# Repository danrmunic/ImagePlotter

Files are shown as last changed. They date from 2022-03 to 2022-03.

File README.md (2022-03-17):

# Image Plotter
__Authors: John Bennett, Daniel Munic, Rudi Diaz__<br />
__Date Modified: March 15, 2022__

This README.md introduces the Image Plotter project, a ME 405 project. It includes the overviews of the implemented hardware and software as well as aa discussion of the results and what we have learned.

## Introduction
We created an image plotter capable of moving a pen with 2.5 degrees of freedom The robot plots in polar (r, theta) coordinates and can turn its operation on and off, by lifting or dropping a pen. We rotate a threaded rod for radial translations and use direct drive to move our wheel around a fixed origin to create the theta angle. A solenoid was used for lifting a pen. We communicate drawing instruction through the serial port from our PC. 

The project is intended to be operated by its creators: John Bennett, Daniel Munic, and Rudi Diaz since we have a deeper understanding of the code. But the device is intended for anyone that wants to use our image plotter. We have a file that converts an image into a printable text file that can be interpreted by our code. So, if anyone has an image, we can print it!

The goal of this project was to create any desired image by generating a series of contours and sending individual commands to the robot until the masterpiece is done. We were able demonstrate that we accomplished this goal by drawing squares, circles and writing the word image.

## Hardware Design Overview
The image plotter hardware that is structural consists of a support bearing, a wooden bearing, a wooden frame, a wooden leg for bearing, and a rod at the origin. The image plotter hardware that is non-structural consists of two Pitterson DC motors, a threaded rod, a direct drive shaft connected to a wheel, a sharpie, a breadboard, a 5A MOSFET, a solenoid, a Nucleo with a shoe, a 2 H-bridge motor driver, a limit switch, and a solenoid and pen carriage. For a full list of our hardware see the BOM below.

### BOM 
| Qty. | Part | Source | Est. Cost | 
|:----:|:---|:---|:---:|
|  2 | Pittperson Gearmotors | ME405 Tub | - |
|  1 | Nucleo with Shoe | ME405 Tub | - |
|  2 | Black Sharpie | Pre-Owned | - |
|  1 | Motor Driver 2 H-bridges  | ME405 Tub | - |
|  1 | 5A Power MOSFETs | [DigiiKey](https://www.digikey.com/en/products/detail/stmicroelectronics/STN3NF06L/654517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) | $3.80 |
|  1 | Diode | ME405 Tub | - |
|  1 | Solenoid Actuator | [Digikey](https://www.digikey.com/en/products/detail/sparkfun-electronics/ROB-11015/6163694) | $4.95 |
|  1 | Limit Switch | Gift | - |
|  1 | 1/4” Guide Rod 12” Long | ME405 Bin | - |
|  1 | 1/4” Threaded Rod 12” Long| ME405 Bin | - |
|  1 | 3” Rubber Wheel | ME405 Bin | - |
|  2 | 3/8 to 1/4 Shaft Coupler  | [amazon](https://www.amazon.com/Stainless-Steel-Screw-Shaft-Coupler/dp/B00KVNA50G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) | $9.98 |
|  1 | Bearing Wheel | Clayton | - |
|  1 | Wooden Bearings | Scrap Wood Bin | - |
|  1 | Wooden Frame | Scrap Wood Bin | - |
|  1 | Wooden Wheel Leg | Scrap Wood Bin | - |
|  1 | Rotating Rod at Origin | ME405 Bin | - |
|  1 | Solenoid and pen platform Carriage | 3D Print | - |

The motors are in charge of moving the solenoid and pen carriage. The pen carriage contains the sharpie and solenoid. One motor controls the radial distance by rotating the threaded shaft. This pushes the solenoid and pen carriage along the shaft at about motor 1000 radians per about 8 inches of radial movement. The solenoid and pen carriage uses the direct drive shaft and wooden bearings to keep movement stable. The second motor controls the angular coordinate by using direct drive to move the wheel around a fixed rod at the origin to create the theta angle, 20 radians on the motor are a 90 degree turn. We are also able to control the pen's linear motion, up and down, by using a solenoid. This allows the device to be able to draw on all areas of the paper. The solenoid is controlled by a MOSFET. When there is a high voltage input, the MOSFET will allow current to flow from 5V to ground. We have a diode in parallel with the solenoid to protect our handwear. The breadboard is used to provide a surface to connect electrical components. We have a limit switch which is mounted close to our motors. the limit switch allows up to locate the origin when the solenoid and pen carriage crash into it. The wooden frame is what everything is mounted to, and it provides support for the entire system. The support bearing adds another contact point to prevent the wooden frame from tilting. See figure 1 and 2 for hardware models. 

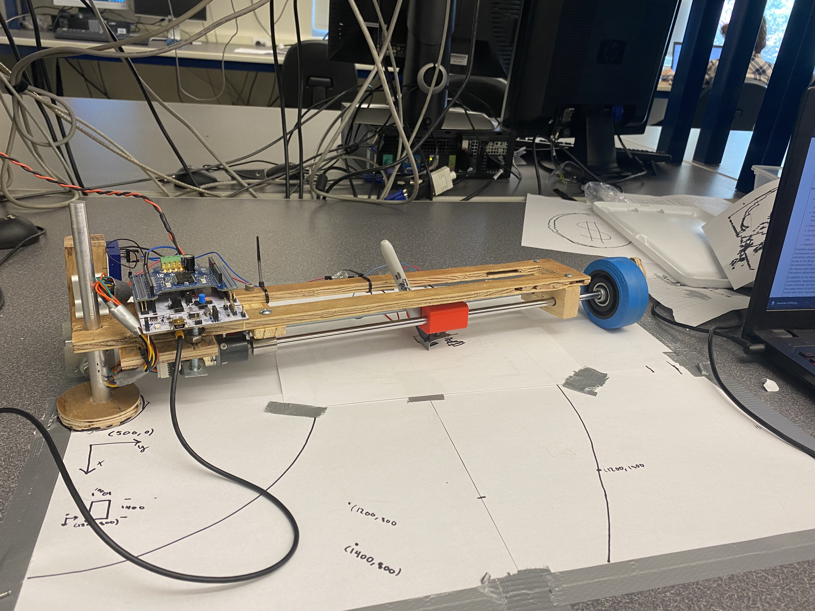
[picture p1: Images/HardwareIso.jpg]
Handwear


__Figure 1:__ Image Plotter Hardware.

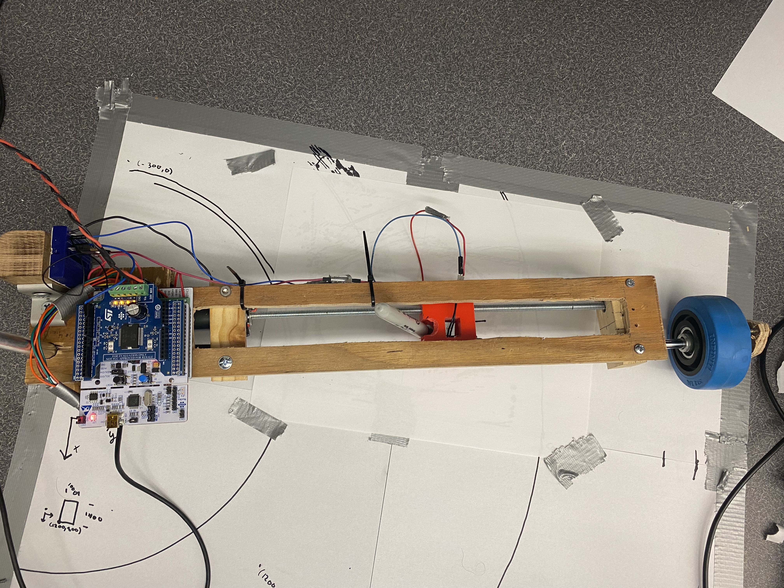
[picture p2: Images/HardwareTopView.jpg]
Top View Handwear


__Figure 2:__ Top View of Image Plotter Hardware.

Figure 3 shows a close-up view of our nucleo and breadboard and shows our wiring layout.

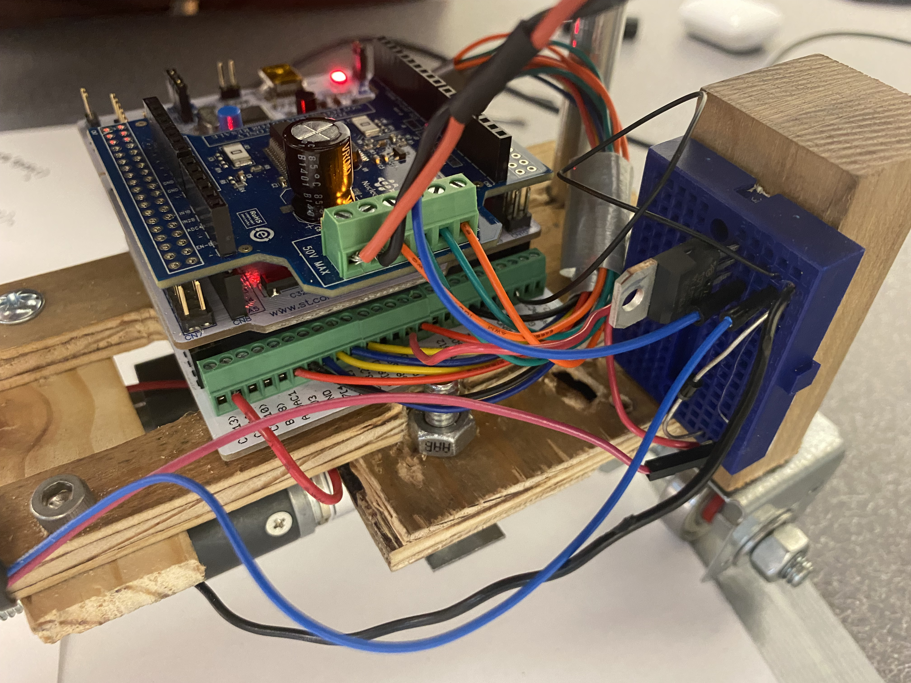
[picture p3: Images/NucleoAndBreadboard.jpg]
Nucleo and Breadboard Layout


__Figure 3:__ Top View of Image Plotter Hardware.

## Software Design Overview
The software ran on the nucleo is designed using a number of generators which operate as tasks scheduled in [main.py](https://github.com/danrmunic/ImagePlotter/blob/main/src/main.py). These tasks are the motor task, user task, logic task, and solenoid task. The code ran in [main.py](https://github.com/danrmunic/ImagePlotter/blob/main/src/main.py) is meant to accept a singular rectangular coordinate from the user and convert them into motor angles. Then the motors will send the solenoid to that location. By using serial port communication, we can continue to send new rectangular coordinates until we have fully drawn a picture. Besides accepting rectangular coordinates,our code will also accept up "{" and down "}" commands to control the solenoid.

The motor task sends both motors to the desired position using a [motor_driver](https://github.com/danrmunic/ImagePlotter/blob/main/src/motor_driver.py) object and [ClosedLoop](https://github.com/danrmunic/ImagePlotter/blob/main/src/closedloop.py) object, as well as receiving the motor position using an [Encoder](https://github.com/danrmunic/ImagePlotter/blob/main/src/Encoder.py) object to check if a movement is finished. The user task receives points from the serial port which are sent from the computer in [PC.py](https://github.com/danrmunic/ImagePlotter/blob/main/src/PC.py) (and generated in [sobel.py](https://github.com/danrmunic/ImagePlotter/blob/main/src/sobel.py)). The logic task does the math to convert those points from rectangular coordinates to values which can be sent to the motors in the polar coordinate system. Finally, the Solenoid task moves the pen up and down while drawing based on input from the computer.  

Variables are shared between tasks using Shares and Queues in [task_share.py](https://github.com/danrmunic/ImagePlotter/blob/main/src/task_share.py)

## Results Overview
Our system was able to draw a successful rectangle, circle, and the word "IMAGE" legibly. These images matched our jpg image. We will describe our testing process as well as the tests we preformed

We first started with calculations to predicted how to move from a rectangular coordinate to motor angles. We needed relationships between motor angles to theta and radius, we got these values experimentally by moving the motors. Next, we checked if the robot could accept polar coordinates. We wanted to determine if the robot could move to the desired polar coordinate. We had to further tune parameters to get the accuracy we wanted. Once we have achieved polar coordinates, we then started inputting rectangular coordinates. Once we were confident in our robot’s ability to move from one point to the next we moved to drawing images. 

The system was first tested by sending a picture of a square. While drawing we noticed that when the machine had to draw short strokes, the machine was able to make precise movements and replicate it onto the paper. However, when we inputted large change in position the machine would have difficulty accurately creating this line. This might be because the machine is working in radial and angular coordinates, so it struggles to be able to make straight lines, since the movement in the theta direction is significantly larger than the radial movement. As we progressed with the project, we were able to change the step size to get the best results. 

We had the system draw three figures. The first was a simple rectangle picture the rectangle was drawn based on the png image in figure 4. Figure 5 shows our machine’s output drawing. As you can see, the image is not a perfect copy of the image in figure 4, this is due to the fact that due to the machine's coordinate system being cylindrical and has large controller gains. This allowed for slight discrepancies as the machine did it's best to copy the image but was unable to make perfect lines. However, the results are still pretty amazing as the image is easily recognizable to the original image.



__Figure 4:__ Png Image of a Rectangle

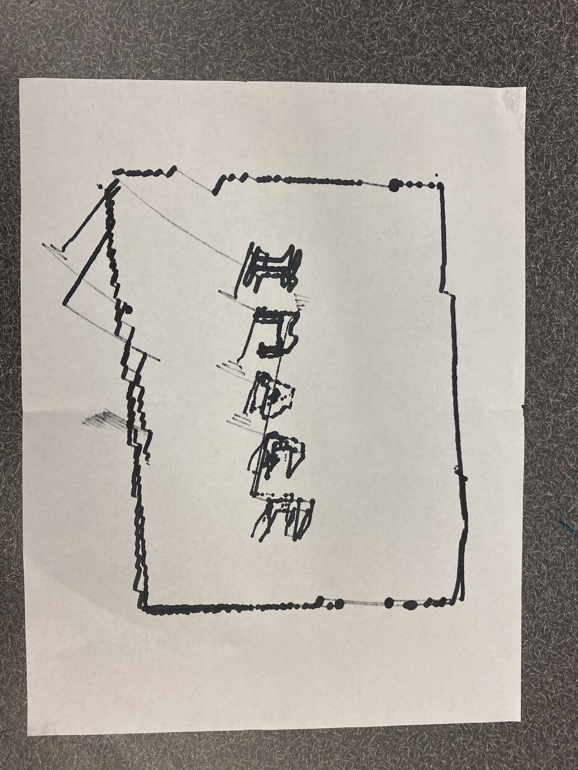
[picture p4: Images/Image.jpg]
Rectangle


__Figure 5:__ System's Drawing of a Rectangle. (Ignore the word image in the center)

We drew another simple shape of a circle. this drawing was also pretty good, but we did not have smooth curves. The scaling of the circle was obviously skewed. See figures 6 and 7. The image looked good and we were extremely happy with these results.

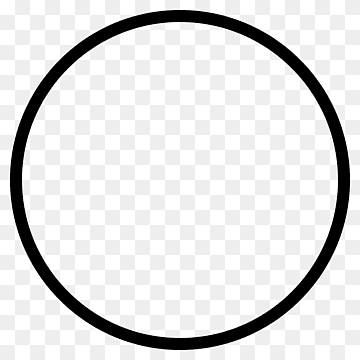
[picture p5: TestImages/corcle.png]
Circle Picture


__Figure 6:__ Png Image of a Circle.

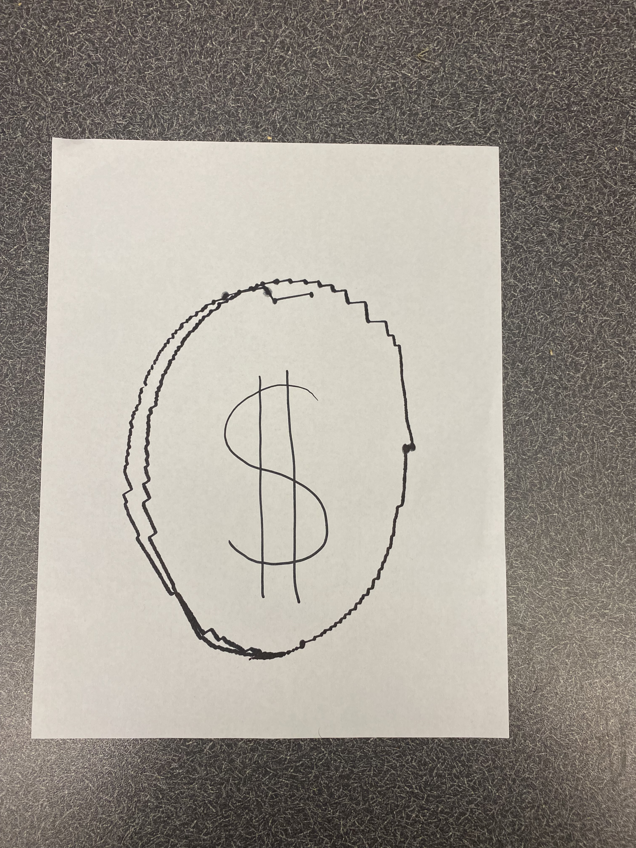
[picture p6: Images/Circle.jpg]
circle


__Figure 7:__ System's Drawing of a Circle.

The next image the machine drew was the word "IMAGE" as seen in figure 8. The drawing created by the robot can be seen in figure 9. Here we can see that the robot was able to replicate the drawing with a surprising amount of accuracy. One drawback was that machine took a large amount of time in order to complete this image as it could not move the pen at high speeds and the movements it made, while precise, were extremely small. We attempted to rectify this issue by having the machine draw every third point it received, but this led to errors, so we removed this feature. 



__Figure 8:__ Png Image of the Word Image.



__Figure 9:__ System's Drawing of the Word Image.

As for the last image, we had the image attempt to draw former US president Barack Obama. This was by far the most detailed image which unfortunately led to being the hardest one to complete. With all the details required, the image created unfortunately was not able to be an exact copy of the image we had. It also took a long time as the machine tried to capture every last detail. Our picture of Obama is unrecognisable.

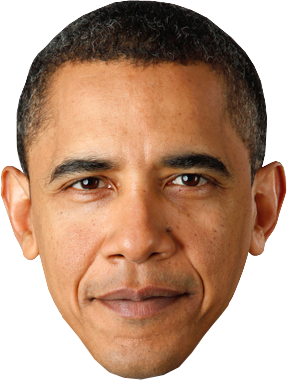
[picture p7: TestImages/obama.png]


__Figure 10:__ Png Image of Obama.

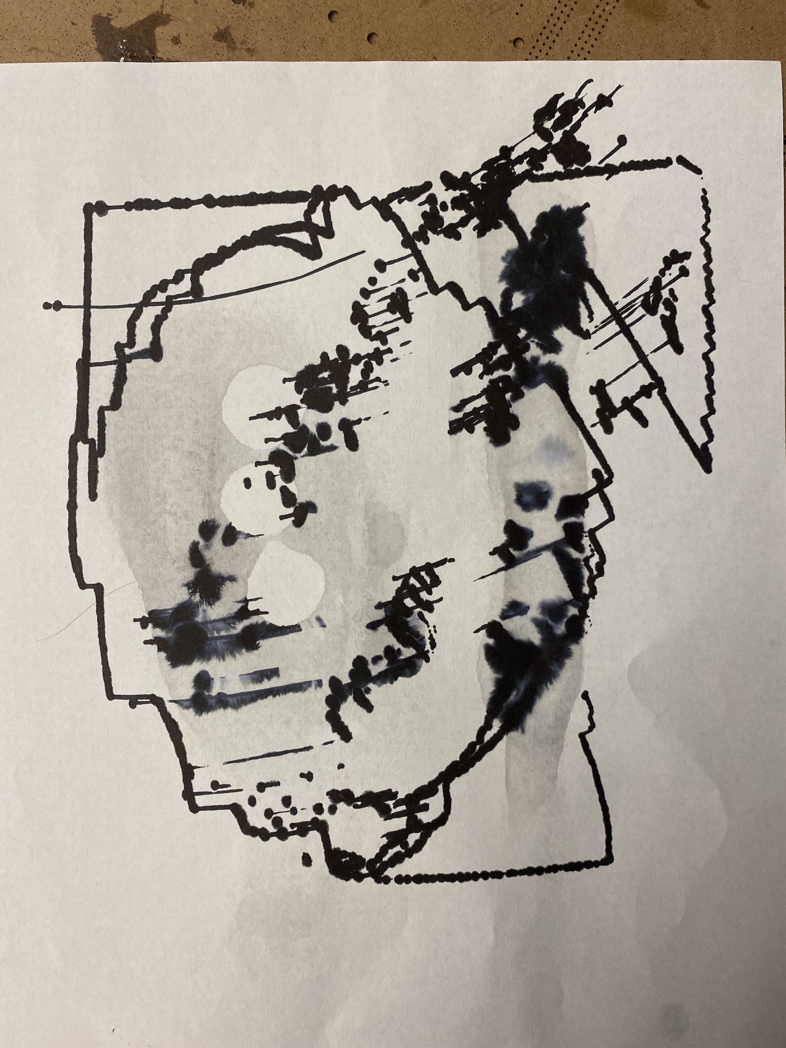
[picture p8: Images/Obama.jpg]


__Figure 11:__ System's Drawing of Obama.

## Expanding on the Process
In this project, we learned how useful it is to have a greater understanding of various components, we learned how to implement a limit switch, and a solenoid into our code. Also gaining experience and exploring different venders of mechatronic devices really opened our eyes to how to design. There were a couple of tough lessons that we learned during this project. The first was that when the robot rotated the motors moved at different speeds this made keeping a straight line difficult. To overcome this, we decreased the step size between movements. The next is that when purchasing an art make sure it can do what we want it to do. The purchased solenoid could not easily attach to the to the pen. There are solenoids that we could have bought with threads to mount stuff, but we failed to check for how it will mount. This error caused us a lot of stress since it took a long time for us to figure out how to hold the pen. Finally, our project was not the most well designed most of the arts were from the scrap bin, but by having good controls, good resolution and a well-tuned system helped to improve our systems performance in our project. 

For anyone who would like to build on our device, we have several recommendations could help. First, improve the way the solenoid is attached to the pen. Currently it is only attached by a quick solder. This allows the pen to rotate while drawing which ruins the accuracy of our lines. If the connection were rigid the pen would be able to draw more accurately. Additional parameter tuning is required to optimize the system the Ki and Kd are currently zero and the motor period and Kp could need more tuning. This would allow the drawing to get to each point more accurately and may even allow a decreased tolerance. Decreasing the number of points in a contour would greatly improve the speed at which the machine prints.  

## Additional files
### Microcontroller Classes

* [main.py](https://github.com/danrmunic/ImagePlotter/blob/main/src/main.py)
* [encoder.py](https://github.com/danrmunic/ImagePlotter/blob/main/src/Encoder.py)
* [motor_driver.py](https://github.com/danrmunic/ImagePlotter/blob/main/src/motor_driver.py)
* [closedloop.py](https://github.com/danrmunic/ImagePlotter/blob/main/src/closedloop.py)
* [task_share.py](https://github.com/danrmunic/ImagePlotter/blob/main/src/task_share.py)

### PC Classes
* [PC.py](https://github.com/danrmunic/ImagePlotter/blob/main/src/PC.py)
* [sobel.py](https://github.com/danrmunic/ImagePlotter/blob/main/src/sobel.py)

### Documentation

* [Image Plotter Documentation](https://github.com/danrmunic/ImagePlotter)

### Website Link

* [Image Plotter Website](https://danrmunic.github.io/ImagePlotter/index.html)

### Solidworks files

* [Solidworks files](https://github.com/danrmunic/ImagePlotter/tree/main/Solidworks%20Model)

### Images Used for Testing

* [TestImages](https://github.com/danrmunic/ImagePlotter/tree/main/TestImages)

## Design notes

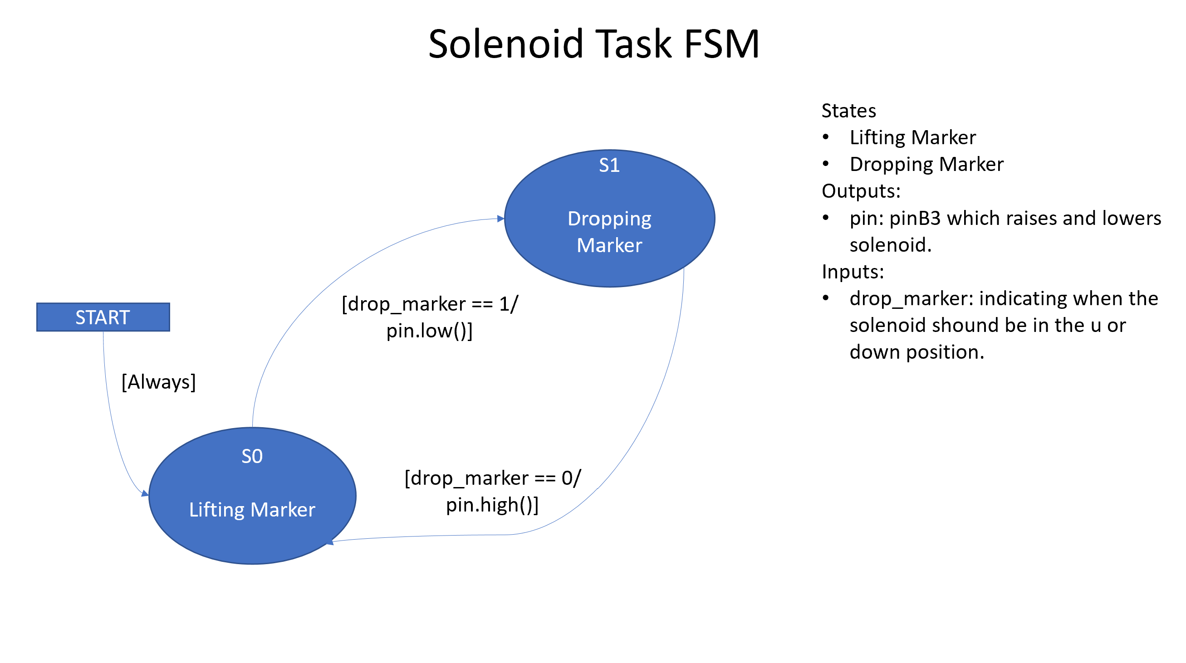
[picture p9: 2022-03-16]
Images/FSMSolenoid.png

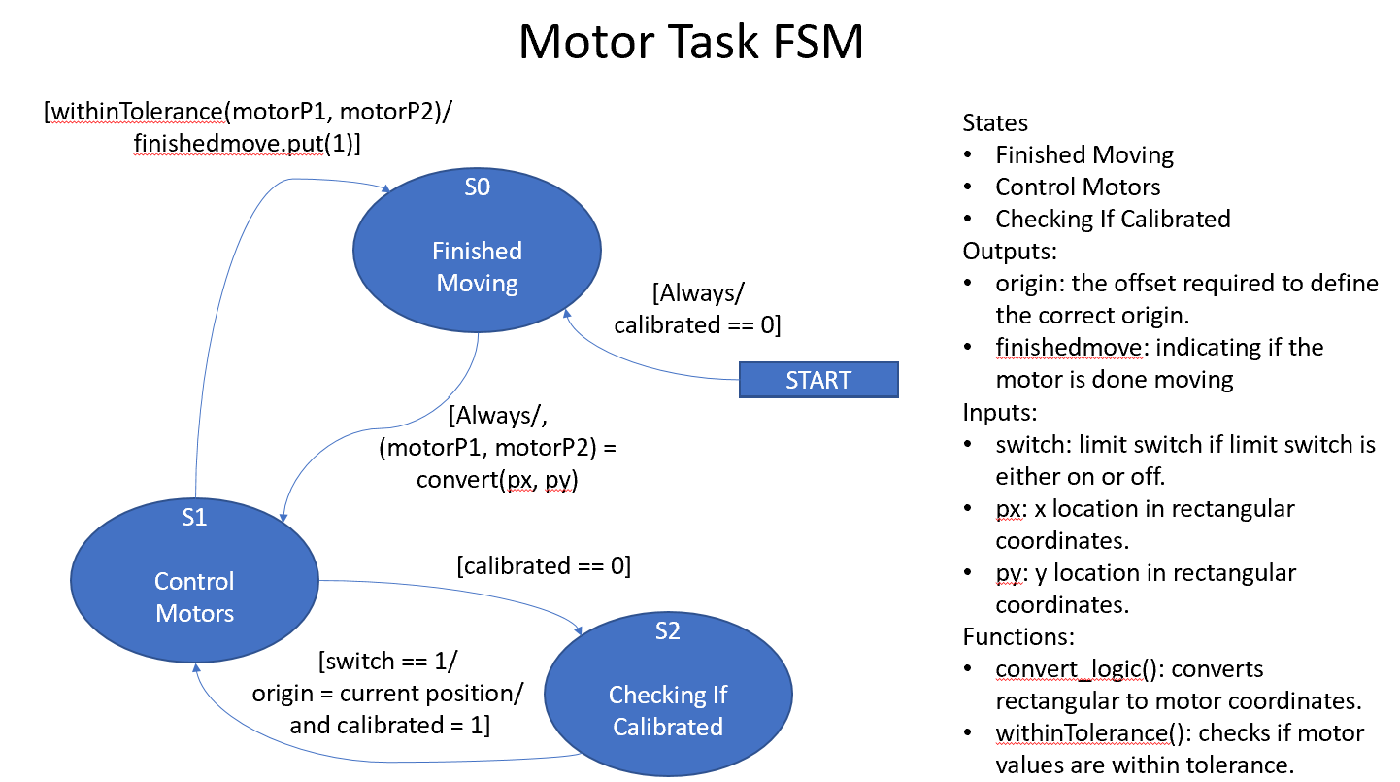
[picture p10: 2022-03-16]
Images/FSMMotors.png

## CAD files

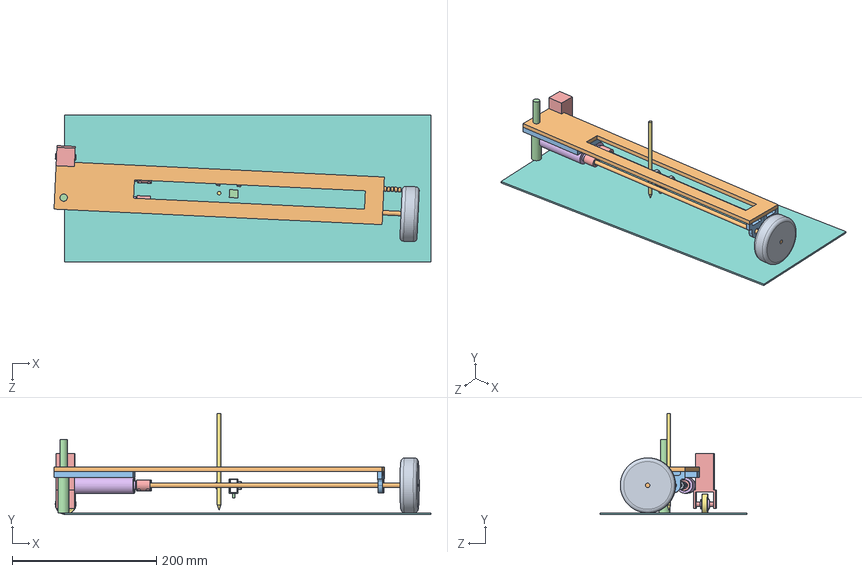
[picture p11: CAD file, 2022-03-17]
Solidworks Model/ImagePlotterFinalAssemble.SLDASM
522.4 x 140.5 x 203.2 mm
wheel
threaded shaft x 2
pillow block x 2
Solenoid
shaft coupler x 2
Patterson Motor x 2
pen
Paper^ImagePlotterFinalAssemble
95462A029_Medium-Strength Steel Hex Nut x 2
Part5^ImagePlotterFinalAssemble
Part1^ImagePlotterFinalAssemble
Part3^ImagePlotterFinalAssemble
Part4^ImagePlotterFinalAssemble
Bearing Spacer
60355K601_Ball Bearing

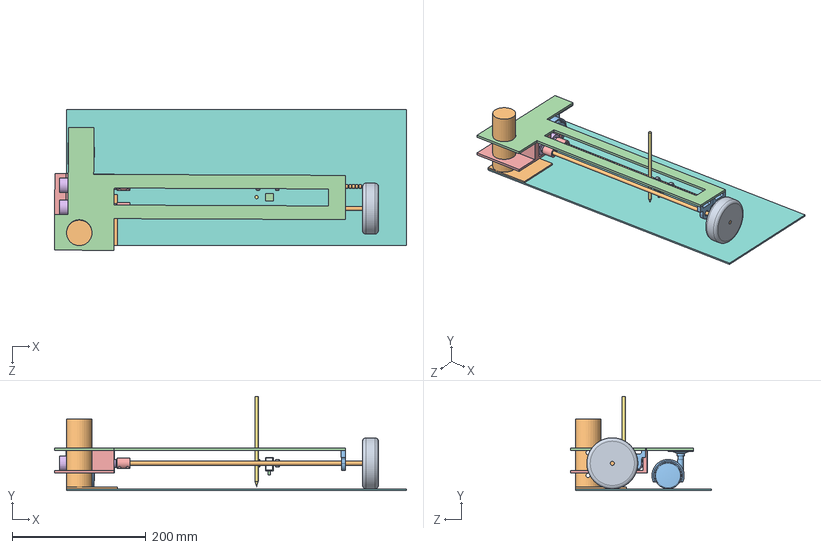
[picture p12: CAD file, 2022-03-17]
Solidworks Model/ImagePlotter.SLDASM
526.0 x 140.5 x 210.3 mm
wheel
threaded shaft x 2
pillow block x 2
Solenoid
shaft coupler x 2
Patterson Motor x 2
pen
Paper^ImagePlotter
95462A029_Medium-Strength Steel Hex Nut x 2
Part3^ImagePlotter
24215T44_Light Duty Furniture Swivel Caster
Part5^ImagePlotter
Part4^ImagePlotter

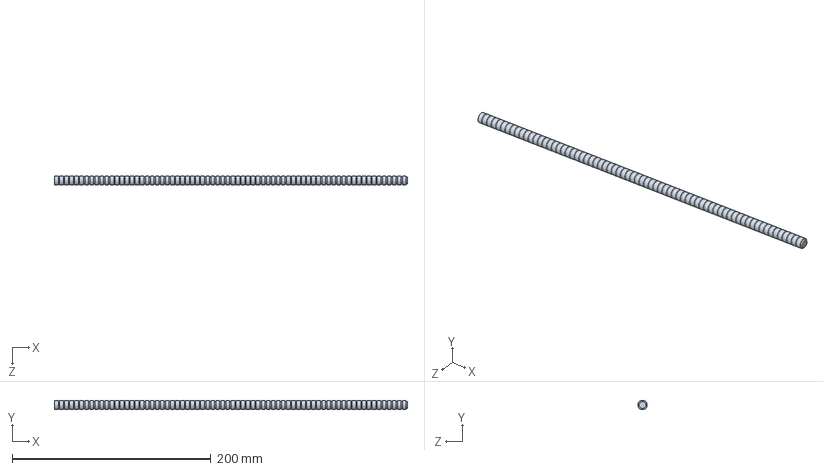
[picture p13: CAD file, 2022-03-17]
Solidworks Model/threaded shaft.SLDPRT
355.6 x 9.53 x 9.53 mm

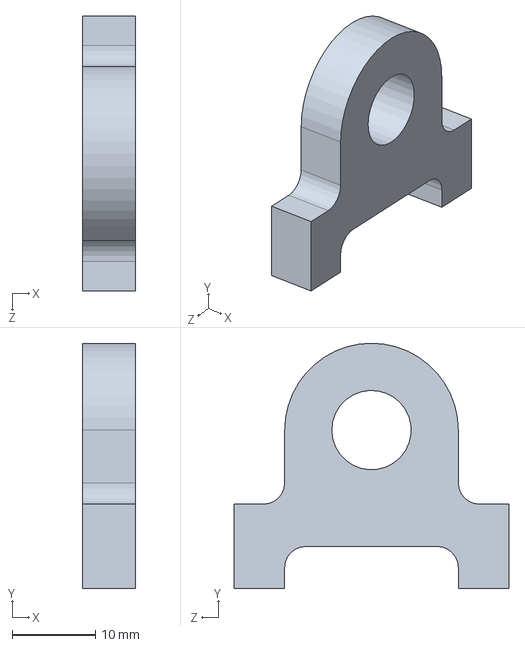
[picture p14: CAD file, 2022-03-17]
Solidworks Model/pillow block.SLDPRT
6.35 x 29.5 x 33.0 mm

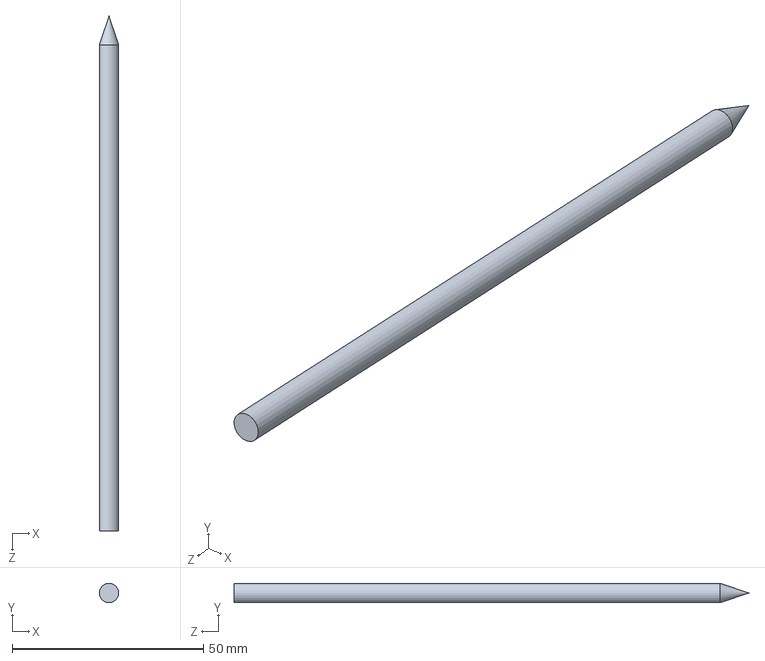
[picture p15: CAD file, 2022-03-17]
Solidworks Model/pen.SLDPRT
5.08 x 5.08 x 134.6 mm

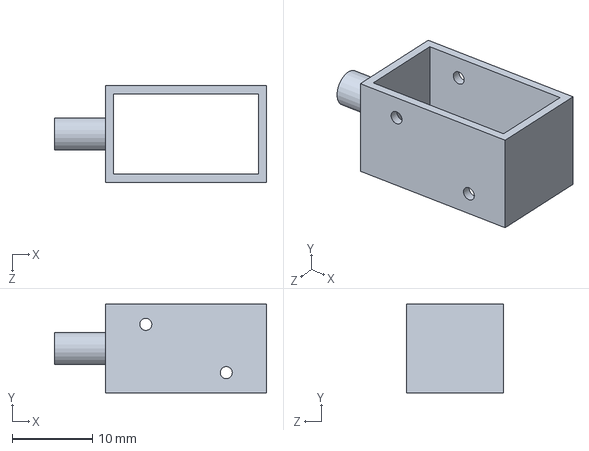
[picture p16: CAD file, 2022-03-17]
Solidworks Model/Solenoid.SLDPRT
26.4 x 11.0 x 12.0 mm

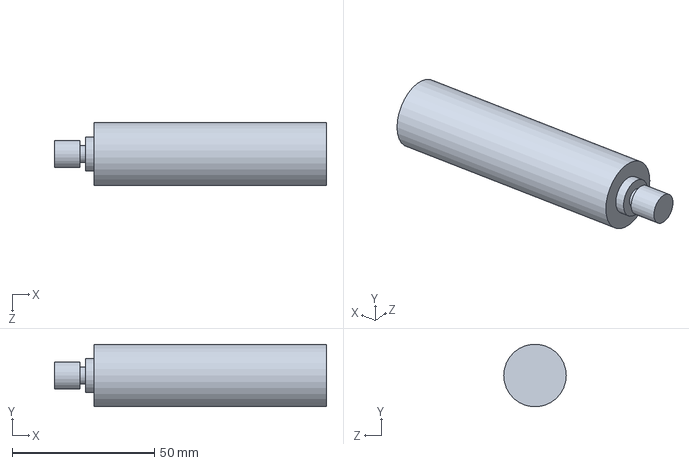
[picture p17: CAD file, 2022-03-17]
Solidworks Model/Patterson Motor.SLDPRT
95.5 x 21.9 x 22.0 mm

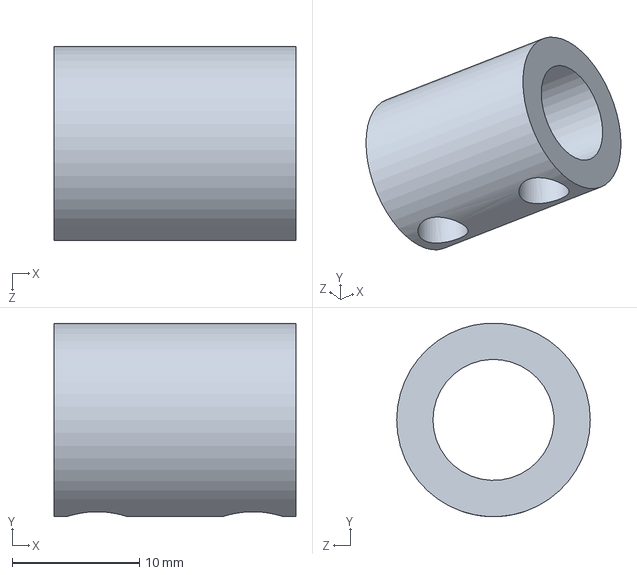
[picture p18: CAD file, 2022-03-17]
Solidworks Model/shaft coupler.SLDPRT
19.1 x 15.2 x 15.2 mm

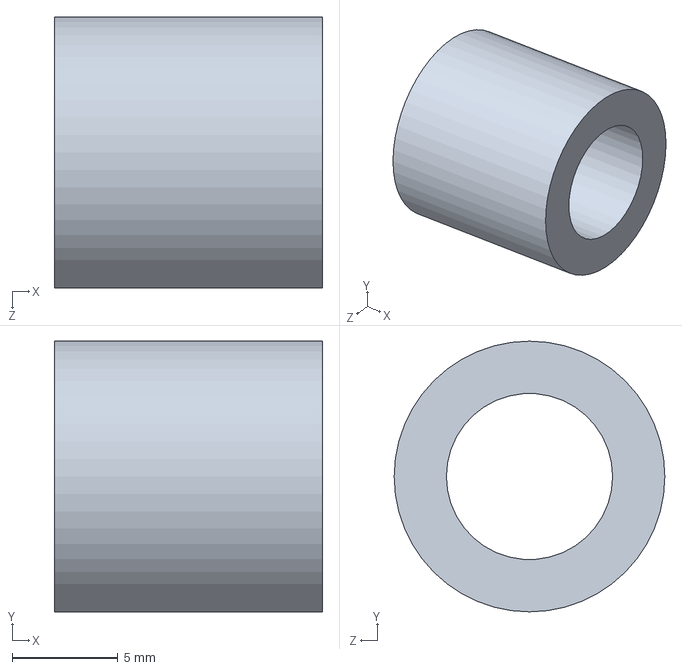
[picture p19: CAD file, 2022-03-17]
Solidworks Model/Bearing Spacer.SLDPRT
12.7 x 12.8 x 12.8 mm

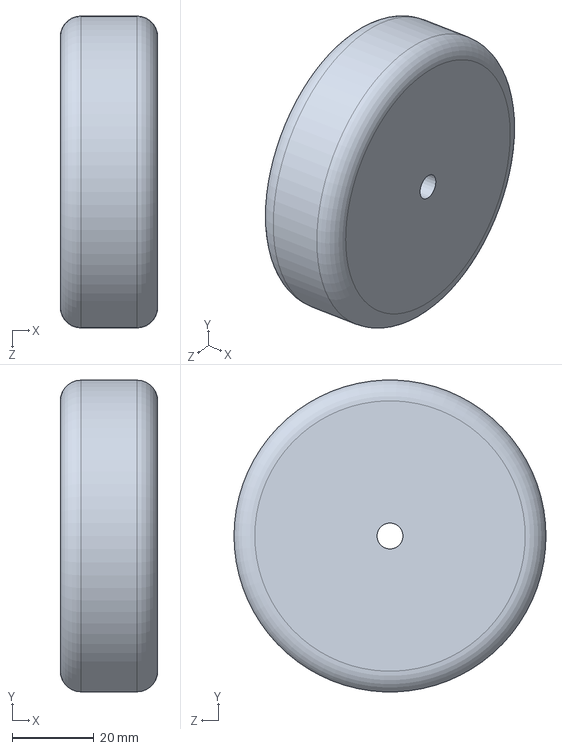
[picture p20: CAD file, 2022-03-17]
Solidworks Model/wheel.SLDPRT
23.8 x 76.1 x 76.2 mm

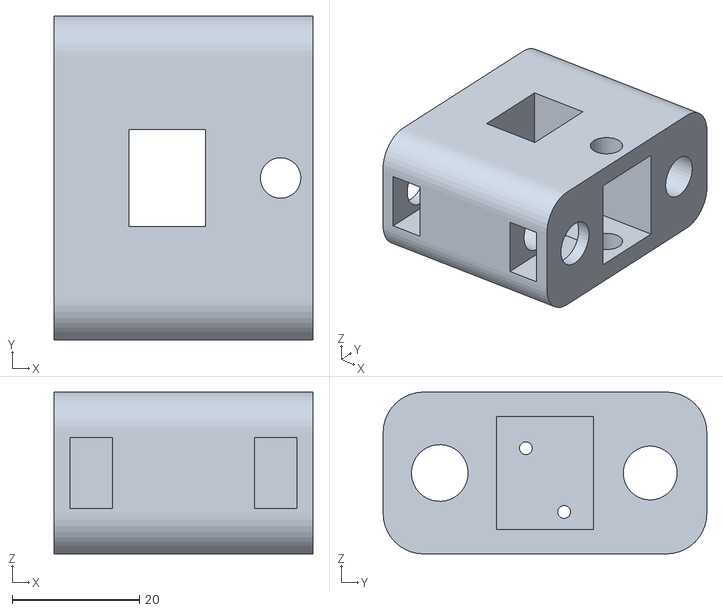
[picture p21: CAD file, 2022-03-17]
Solidworks Model/SolinoidCarriage.STL
40.6 x 50.8 x 25.4

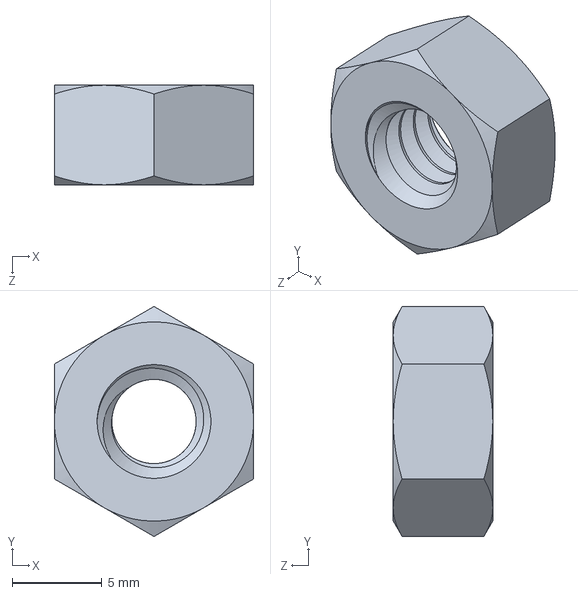
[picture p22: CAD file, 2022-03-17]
Solidworks Model/95462A029_Medium-Strength Steel Hex Nut.SLDPRT
11.1 x 12.8 x 5.56 mm

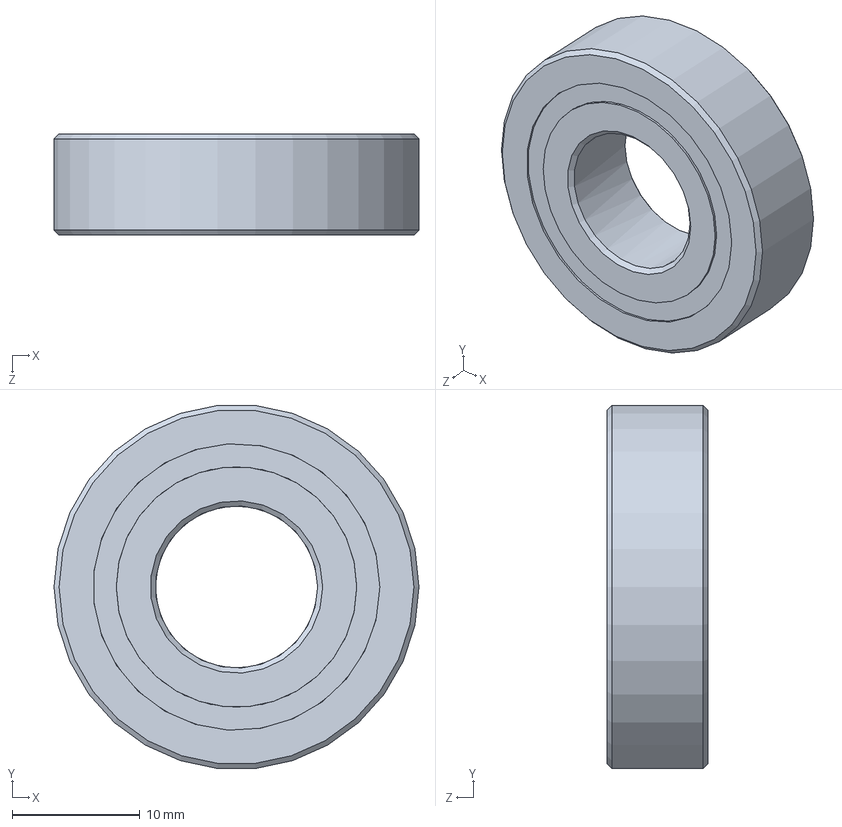
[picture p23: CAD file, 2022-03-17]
Solidworks Model/60355K601_Ball Bearing.SLDPRT
28.6 x 28.4 x 7.94 mm

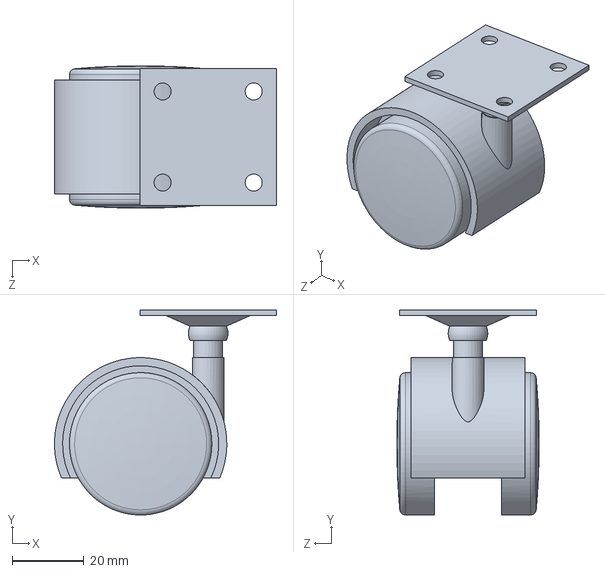
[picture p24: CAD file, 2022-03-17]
Solidworks Model/24215T44_Light Duty Furniture Swivel Caster.SLDPRT
61.9 x 57.1 x 39.7 mm

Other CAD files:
Solidworks Model/ImagePlotterV2.SLDASM
Solidworks Model/Bearing Spacer.STL

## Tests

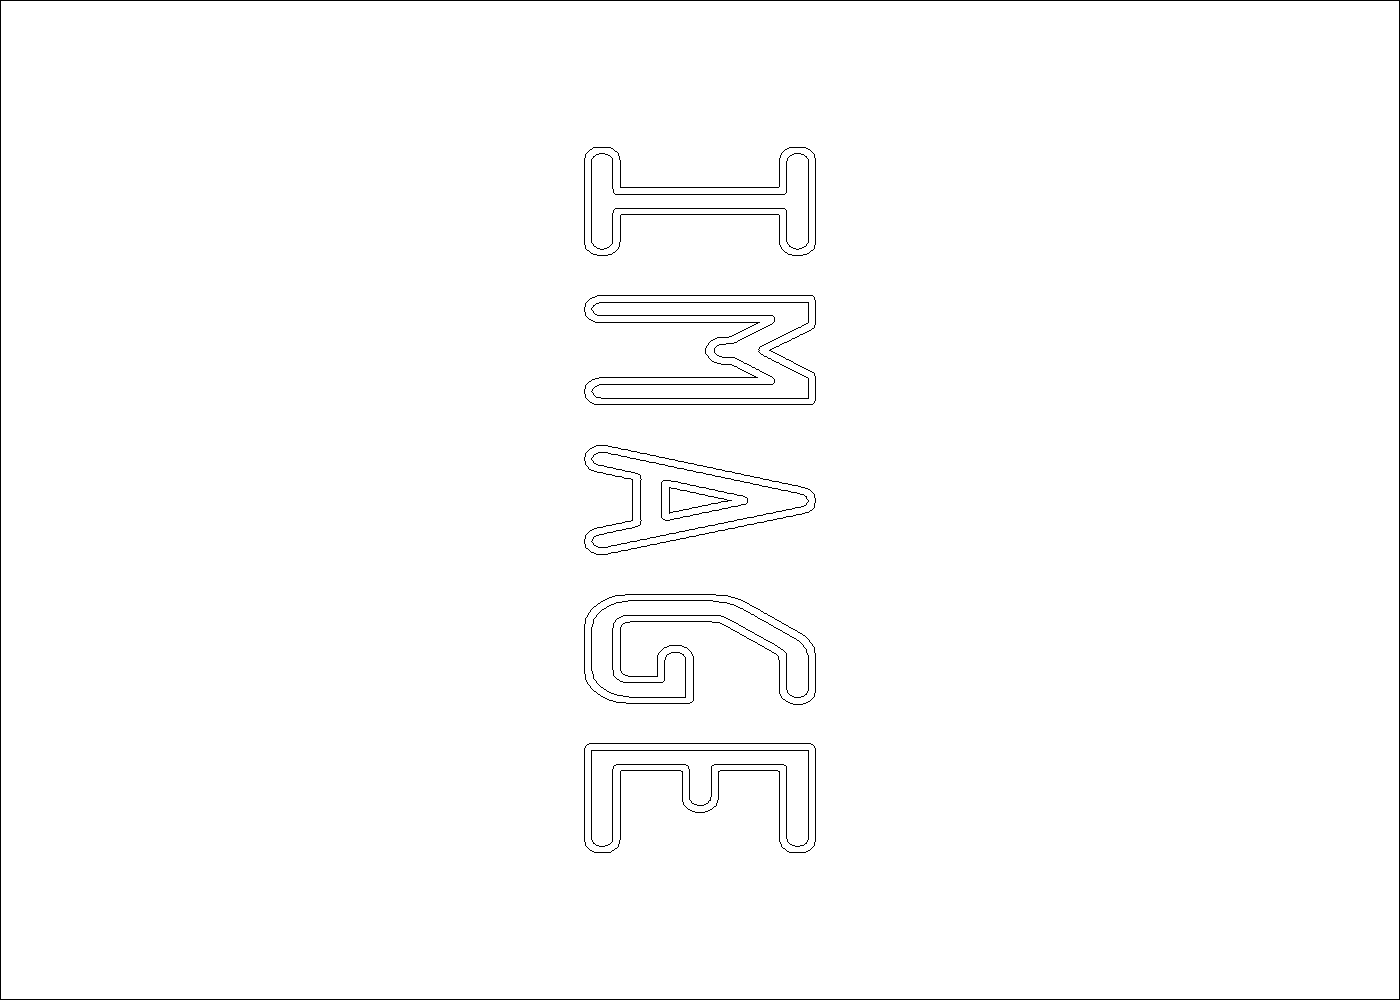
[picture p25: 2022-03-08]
TestImages/image(output).png

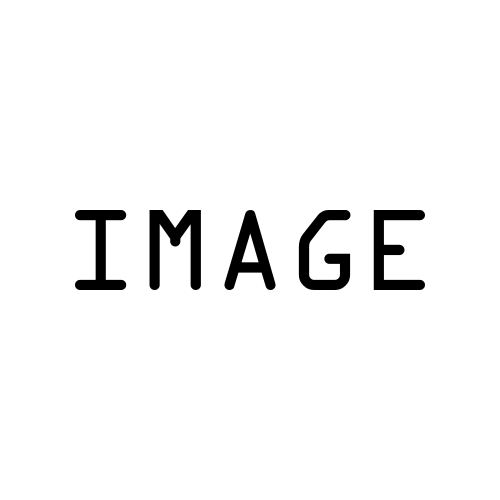
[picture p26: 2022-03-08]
TestImages/image.png

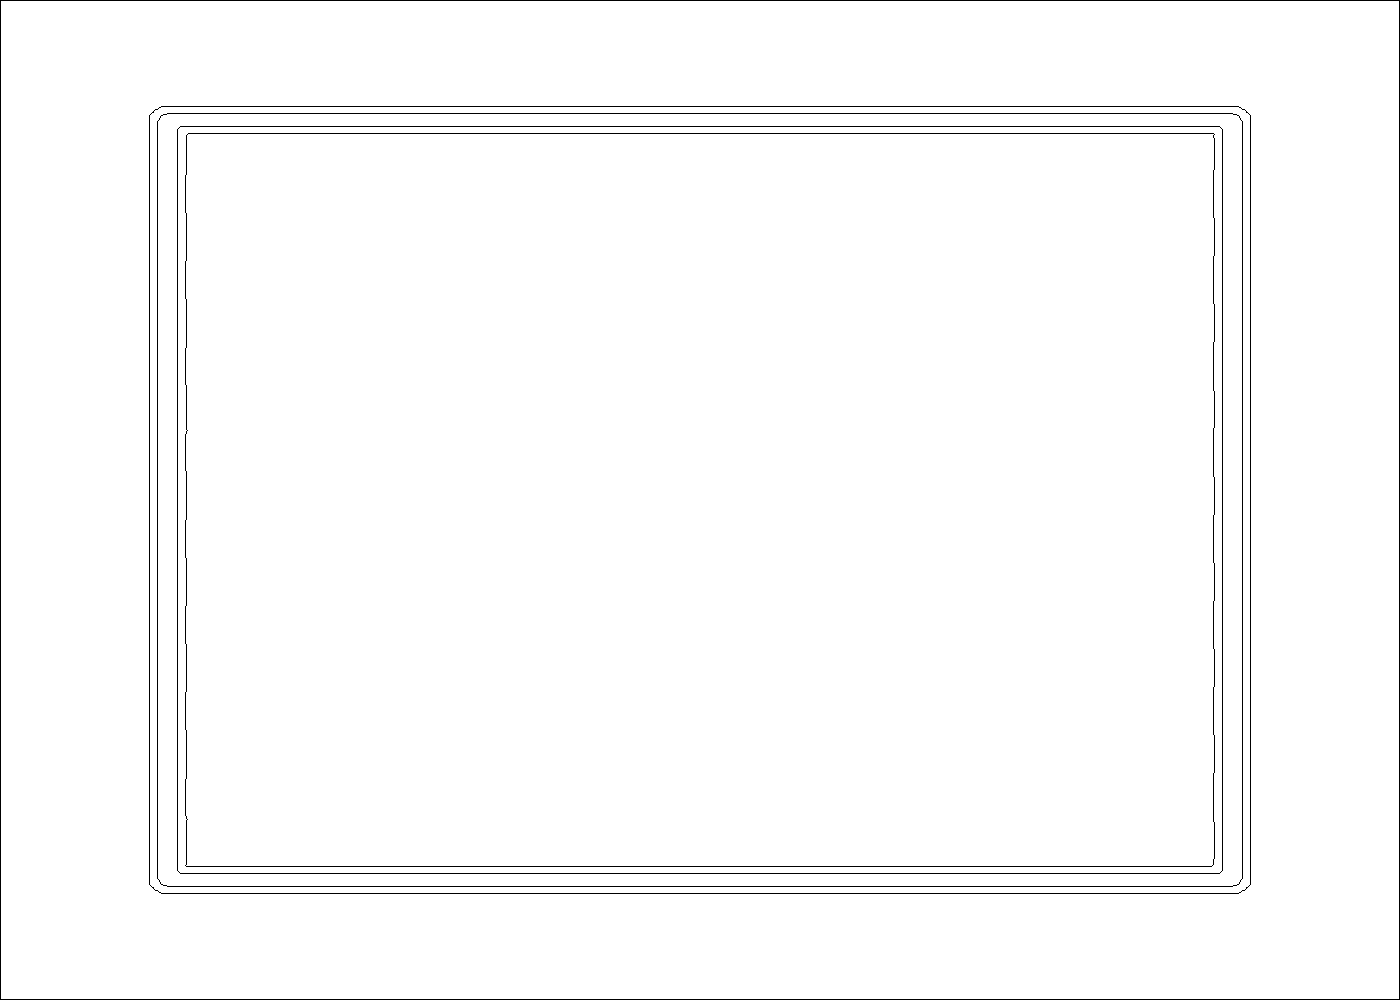
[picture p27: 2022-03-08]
TestImages/square(output).png

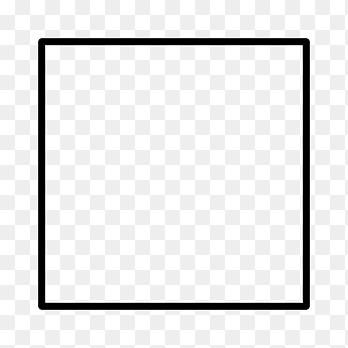
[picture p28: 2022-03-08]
TestImages/square.png

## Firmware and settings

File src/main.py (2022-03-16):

"""!
    @file main.py
    @brief Runs main logic of the image plotter and loops through tasks
    @details The goal of main.py is to be able to lot between point that were sent over serial. This file contains a program that runs through 3 tasks User task, motor task and a solinoid task. We use cotask to schedule each task.  
    @author Rodi Diaz
    @author Daniel Munic
    @author John Bennett
    @date March 15, 2022   
"""

import gc
import pyb
import cotask
import task_share
import motor_driver
import closedLoop
import Encoder
import math

#selected zero position of the motor
#i.e if you start the program by going to radius = 0, motor1 will move to the origin
#ORIGIN = -1000

class Switch:
    '''!@brief A Switch class used to read the status of a switch.
    '''
    def __init__ (self, inpin):
        '''!@brief Initializes switch object.
            @param pin used for switch
        '''
        ## pin object
        self.pinSwitch = pyb.Pin (inpin, pyb.Pin.IN, pyb.Pin.PULL_UP)
    def state(self):
        '''!@brief Read Status of switch
        '''
        if self.pinSwitch.value()==1:
            return 1
        return 0

def polar_to_motor(point):
    '''!@brief function that converts our point into a value acceptable for the motors.
        @details This function takes our two points, which are in the (R,theta) axis and
        maps these values into a certain region. The conversion is done so that the motors
        don't overextend and cause the machine to push pass its limits.
        @param point is the position of the motors in an (R,theta) axis
    '''     
    #input is in the format (r, theta)
    #motor 2 goes from -10 to 10, which is 90 degrees
    #motor 1 goes from 0 to 1000, which is 8.75 inches
    #theta goes from -pi/4 to pi/4
    #r goes from 0 to sqrt(1000^2+ 500^2) ~~1118
    
    r = point[0]
    theta = point[1]
    
    #map the values from 0 to 1118 into -900 to 100
    th1 = (r * 1000/math.sqrt(1000**2 + 500**2)) + origin.get() -650
     
    #map the values from -pi/2 to pi/2 into -10 to 10
    th2 = ((theta) * 10) / (math.pi/4)
    
    return (th1,th2)


def rectangular_to_polar(point):
    '''!@brief function that converts our point int cylindrical system.
        @details This function takes our two points, which are in the XY axis and
        convert these position into a cyldrical coordinate system since our machine moves
        by theta or radial position. The conversion is by the equations, and then returns
        two values, a radius and theta
        @param point is the position of the motors in an (X,Y) axis
    '''    
    #input is in the format (x, y)
    #the image size should be (727, 1000)
    x = point[0]
    y = point[1]
    
    #cartesian coordinates before transforming the image (x,y):
    #                        o
    #(0,1000)________________(0,0)
    #        |               |
    #        |               |
    #        |               |  O
    #        |               |
    #        |_______________|
    #(1000,1000)             (1000, 0)
    #O is the robot aka the reference we will be taking the angle from
    #o is the reference the computer is taking for the points
    
    #cartesian coordinates after transforming the image (newx,newy):
    #(600,-500)________________(1600,-500)
    #        |               |
    #        |               |
    #(0,0)O  |               |
    #        |               |
    #        |_______________|
    #(600, 500)                 (1600, 500)
    
    #polar coordinates (r, theta)
    #(500,-pi/2)________________ (1118,arctan(-500,1000))
    #            |               |
    #            |               |
    #         O  |               | (1000, 0)
    #            |               |
    #            |_______________|
    #(500, pi/2)                  (1118, arctan(500/1000))
    
    #rotate the point 90 degrees using rotation matrix
    #newx = cos(pi/2) x + sin(pi/2) y
    #newy = -sin(pi/2) x + cos(pi/2) y
    #Add 600 to newx because of the distance between r=0 and the lever point
    newx = y
    newy = -x
    
    #transform the image so our 'angle reference point' is in the middle
    newy = newy + 500
    
    #print("transformed rectangular:" + str((newx, newy)))
    
    #calculate r and theta of the new image
    #handle divide by zero
    if newx == 0.0:
        newx = 0.00001
    theta = math.atan(newy/newx)
    r = math.sqrt(newx ** 2 + newy ** 2)
    
    rsatLim = [800,1950]
    if r<rsatLim[0]:
        r = rsatLim[0]
    elif r>rsatLim[1]:
        r = rsatLim[1]
    
    thsatLim = [-3.14159/2,3.14159/2]
    if theta<thsatLim[0]:
        theta = thsatLim[0]
    elif theta>thsatLim[1]:
        theta = thsatLim[1]
    
    return (r,theta)

def convert_logic (px,py):
    '''!@brief function that moves between the states.
        @details This function takes the location of the current position. It then converts
        this position from rectangular coordiantes into cylindrical. It then sends these values
        to the motors so that it can move the position of the pen.
        @param px is the rectangular coordinate x
        @param py is the rectangular coordinate y
        @return nextpoint is a tupil containing the motor output
    '''   
    next_point = (px, py)
        
    #do the math to find what need to be sent to the motors
    next_point = rectangular_to_polar(next_point)

    next_point = polar_to_motor(next_point)
        
    #send these values to the motors
    return next_point


def task_motor ():
    '''!@brief Initializes and controls two motor to move in olar coordinates.
        @details The motors are first initialized, which involves creating two motor driver, two encoder, and two closed loop controller objects and a switch object.
                The rectangular coordinates are converted to polar and sent to the motor drivers.
                Once the encoder reads that the motors have reached the positions they're supposed to be at,
                the task outputs that the move is finished so the User Task can read the next point. We use a switch to calibrate our motors.
#  
    '''
    ## motor 1 timer (3)
    tim3 = pyb.Timer(3, freq = 20000)
    ## motor 1 pin B4
    pinB4 = pyb.Pin(pyb.Pin.cpu.B4)
    ## motor 1 pin B5
    pinB5 = pyb.Pin(pyb.Pin.cpu.B5)
    ## motor 1 pin Enable Pin A10
    pinENA = pyb.Pin(pyb.Pin.cpu.A10, pyb.Pin.IN, pull = pyb.Pin.PULL_UP)
    ## motor 1 object
    motor1 = motor_driver.Motor_Driver(pinB4, pinB5, tim3, pinENA)
    
    # encoder 1
    ## encoder 1 pin B6
    pinB6 = pyb.Pin.cpu.B6
    ## encoder 1 pin B7
    pinB7 = pyb.Pin.cpu.B7
    ## motor 1 encoder object
    encoder1 = Encoder.Encoder(pinB6, pinB7, 4)
    ## motor 1 controler object
    control1 = closedLoop.ClosedLoop(90)
    
    # motor 2
    ## motor 2 timer (5)
    tim5 = pyb.Timer(5, freq = 20000)
    ## motor 2 pin A0
    pinA0 = pyb.Pin(pyb.Pin.cpu.A0)
    ## motor 2 pin A1
    pinA1 = pyb.Pin(pyb.Pin.cpu.A1)
    ## motor 2 pin Enable Pin C1
    pinENB = pyb.Pin(pyb.Pin.cpu.C1, pyb.Pin.IN, pull = pyb.Pin.PULL_UP)
    ## motor 2 object
    motor2 = motor_driver.Motor_Driver(pinA0, pinA1, tim5, pinENB)
    
    # encoder 2
    ## motor 2 encoder pin C6
    pinC6 = pyb.Pin.cpu.C6
    ## motor 2 encoder pin C7
    pinC7 = pyb.Pin.cpu.C7
    ## motor 2 encoder object
    encoder2 = Encoder.Encoder(pinC6, pinC7, 8)
    ## motor 2 controler object
    control2 = closedLoop.ClosedLoop(200,satLim = [-60,60])
    ## switch object
    switch = Switch(pyb.Pin.board.PC2)
    
    calibrated = 0
    
    #currpos are the positions the motors are currently moving towards (not where they actually are)
    currpos1 = 0
    currpos2 = 0
    tolerance1 = 3.0
    tolerance2 = 1
    while True:
        
        motor1.set_duty(control1.update(encoder1.read(),10))
        motor2.set_duty(control2.update(encoder2.read(),10))
        encoder1.updatePosition()
        encoder2.updatePosition()
        
        #for calibration
        if switch.state() == 1 and calibrated == 0:
            origin.put(encoder1.read())
            print("Calibrated. Origin: " + str((encoder1.read(), encoder2.read())))
            finishedmove.put(1)
            calibrated = 1

            
            
        if finishedmove.get() == 1:
            (currpos1, currpos2) = convert_logic (px.get(),px.get())
            
            control1.set_setpoint(currpos1)   
            control2.set_setpoint(currpos2)
            
            finishedmove.put(0)

        #check the encoder if we're done moving with +- tolerance
        if finishedmove.get() == 0 and currpos1 < encoder1.read() + tolerance1 and currpos1 > encoder1.read() - tolerance1 and currpos2 < encoder2.read() + tolerance2 and currpos2 > encoder2.read() - tolerance2:
            finishedmove.put(1)
            
        yield (0)

def task_user ():
    '''!@brief Task that reads user inputs 
        @details Function that reads user inputs. If the user inputs a piont then the px and py will be updated.
                 If there is a { then the soliniod will raise. If there is a } then the soliniod will drop.
    '''       
    #Reads a file, makes the list of contours out of that
    CommReader = pyb.USB_VCP()
    
    while True:
        if(finishedmove.get() == 1):

            if(CommReader.any()):
                #Reads Most recent Command
                #point format [float,float]
                ## Stores the most recent key pressed
                point = CommReader.readline().decode("UTF-8")
                CommReader.read()
                print("Inputting to serial: " + str(point))

                if '}' in point:
                    print("Lifting Marker")
                    drop_marker.put(0)
                elif '{' in point:
                    print("Dropping Marker")
                    drop_marker.put(1)
                else:
                    try:
                        floatpoint = eval(point)
                        intpoint = (int(floatpoint[0]), int(floatpoint[1]))
                        #this is hacky code below, change this once its all working
                        px.put(floatpoint[0])
                        py.put(floatpoint[1])
                    except (NameError,SyntaxError) as e:
                        print("Wrong point format")
            else:     

                print("READY")
        yield (0)
            
        
def task_solenoid ():
    '''!@brief task that controls the solenoid.
        @details Everytime this function is called, it eiher moves the solenoid back into
        its original posittion or shrinks it. This allows the machine to decide when to write
        on the paper and when not to.
    '''    
    #Control the lifting of the marker
    #I know this doesn't need to be its own task,
    #    but I think its more readable this way than putting it inside the logic task
    pinB3 = pyb.Pin(pyb.Pin.cpu.B3, pyb.Pin.OUT_PP)
#     timer = pyb.Timer(2,freq=50)
#     channel = timer.channel(2,pyb.Timer.PWM,pin=pinB3)
#     channel.pulse_width_percent(0)
    while True:
        if drop_marker.get() == 1:
            pinB3.low()
        else:
            pinB3.high()
        yield(0)

# This code creates a share, a queue, and two tasks, then starts the tasks. The
# tasks run until somebody presses ENTER, at which time the scheduler stops and
# printouts show diagnostic information about the tasks, share, and queue.
if __name__ == "__main__":
    
    global contours
    
    contours = []
    
    while True:
        try:
            print ('\033[2J________Running________ \r\n')
            
            
            ## px rectangular coordinate x read from set by user and read by motor task
            px= task_share.Share ('f', thread_protect = False, name = "px")
            ## py rectangular coordinate y read from set by user and read by motor task
            py= task_share.Share ('f', thread_protect = False, name = "py")
            px.put(500)
            py.put(800)
            
            ## orgin used to correct our encoder values so that we can find the orgin of the coordinate system 
            origin = task_share.Share ('f', thread_protect = False, name = "origin")
            origin.put(-3000)
            
            ## drop_marker booleans for when to rais and lower the marker
            drop_marker = task_share.Share ('b', thread_protect = False, name = "drop_marker")
            drop_marker.put(0)
            
            ## finishedmove booleans for the motor is done moving
            finishedmove = task_share.Share ('b', thread_protect = False, name = "finishedmoved")
            finishedmove.put(1)
                        
            # Create the tasks. If trace is enabled for any task, memory will be
            # allocated for state transition tracing, and the application will run out
            # of memory after a while and quit. Therefore, use tracing only for 
            # debugging and set trace to False when it's not needed
            
            ## Creates motor1 task
            task_motor = cotask.Task (task_motor, name = 'Task_Motor', priority = 1, 
                             period = 40, profile = True, trace = False)
            ## Creates user task
            task_user = cotask.Task (task_user, name = 'Task_User', priority = 1, 
                                 period = 100, profile = True, trace = False)
            
            ## Creates solenoid Task
            task_solenoid = cotask.Task (task_solenoid, name = 'Task_Solenoid', priority = 1, 
                                 period = 100, profile = True, trace = False)
            
            
            # Add all the above tasks to the task list
            cotask.task_list = cotask.TaskList()
            cotask.task_list.append (task_motor)
            cotask.task_list.append (task_user)
            cotask.task_list.append (task_solenoid)
            
            # Run the memory garbage collector to ensure memory is as defragmented as
            # possible before the real-time scheduler is started
            gc.collect ()
            
            # Run the scheduler with the chosen scheduling algorithm. Quit if any 
            # character is received through the serial port
            while True:
                cotask.task_list.pri_sched ()
            
            # Print a table of task data and a table of shared information data
            #print ('\n' + str (cotask.task_list))
            #print (task_share.show_all ())
            #print (task1.get_trace ())
            #print ('\r\n')
        except KeyboardInterrupt:
                break
            
    print('Program Terminating')

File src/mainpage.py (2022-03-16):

"""!
@file mainpage.py
@author Rodolfo Diaz
@author Daniel Munic
@author John Bennett
@date March 15, 2022   
@mainpage

@section Software Software Design
The software ran on the nucleo is designed using a number of generators which operate as tasks scheduled in main.py.
These tasks are the motor task, user task, logic task, and solenoid task.
The code ran in main.py is meant to accept a singular rectangular coordinate from the user and convert them into motor angles.
Then the motors will send the solenoid to that location.
By using serial port communication, we can continue to send new rectangular coordinates until we have fully drawn a picture.
Besides accepting rectangular coordinates,our code will also accept up "{" and down "}" commands to control the solenoid.
First we have all our task diagram and how they interact and share varables.<br>
\image html TaskDiagrams.png "Figure 1: Image Plotter Task Diagram" <br>
The task diagram shows our 3 different tasks and how they communicate. 
The User task sends the x and y coordinates of the next point to the motor task.
The Motor task sends whether the robot is finished moving to the User task
The User task sends whether to drop or lift the marker to the Solenoid task. 
Next sections show each States State Transition Diagram.
@subsection User User Task
\image html FSMUser.png "Figure 2: UserTask State Transition Diagram" <br>
This is the User Task which describes the task the microcontroller runs to take input from the computer through the serial bus.

Input is sent line by line in the form of points (rectangular coordinates) and brackets indicating
control of the solenoid ([ means drop the marker, ] means lift the marker). This can be seen in the text files in the TestImages folder on github. The series of points and brackets
to control the robot is generated in sobel.py. The files are sent in PC.py, which is run by the computer during runtime of the system.

On the microcontroller side, this task waits for input and interperets it (using the built in python function eval to convert strings to float tuples)to be used by other tasks. 
When the robot is ready for another input (when it finished the current function i.e move to a point or drop/raise solenoid) it replies "READY" to the computer. 
@subsection Motor Motors Task
\image html FSMMotors.png "Figure 3: Motor State Transition Diagram" <br>
This is the Motor task. The motors are first initialized, which involves creating two motor driver, two encoder, and two closed loop controller objects.
The rectangular coordinates are converted to polar and sent to the motor drivers.
Once the encoder reads that the motors have reached the positions they're supposed to be at, the task outputs that the move is finished so the User Task can read the next point.
We also have a switch that allows us to calibrate the motor so it knows its current position.
@subsection Solenoid Solenoid Task
\image html FSMSolenoid.png "Figure 4: Solenoid State Transition Diagram" <br>
This is the Solenoid task which moves the marker up and down using the solenoid. This simple task takes input from the User task as a boolean for turning on and off the solenoid. 
@subsection Classes
This section has in depth descriptions of each class.

motor_driver.py contains the Motor_driver class which uses an input duty cycle and Timer to control a motor at the given pins. The duty cycle values are bounded from -100 to 100 percent, negative numbers being an opposite spin direction to positive numbers.  

Encoder.py contains the Encoder class which reads the motor encoder at the given pin at a given interval using a timer. The position is output in radians from the function Encoder.read().

closedLoop.py contains the ClosedLoop class which sets up a PID controller using the given Kp (proportional gain). This controller finds the error between the current and reference value of the motor to update the duty at which the motor will be run for correction. 

sobel.py uses the openCV library to convert an image to a series of points, sorted by contours (adjacency for the robot to draw continously). This is done using a sobel filter to find the image gradient and then thresholding those values and finding the contours of the image to draw a rough sketch of it.

Pc.py reads a text file (generated by sobel.py) and outputs (through the serial bus) one line every time the string READY is recieved from the serial bus. 

task_share.py contains Share and Queue classes which allow tasks to share data.

cotask.py contains the classes Task and Tasklist which allow classes to run cooperatively.
"""

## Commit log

2022-03-06 Combined motor tasks
2022-03-15 most current push
2022-03-16 the letter next to o and [ broke on my key board
2022-03-17 solid stuff!
    [24215T44_Light Duty Furniture Swivel Caster.SLDPRT, 60355K601_Ball Bearing.SLDPRT, 95462A029_Medium-Strength Steel Hex Nut.SLDPRT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]
